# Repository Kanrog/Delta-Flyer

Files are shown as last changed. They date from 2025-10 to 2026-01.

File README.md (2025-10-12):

# Delta Flyer Refit Website

This is the website for the Delta Flyer Refit 3D printer project, designed by Rolohaun and Kanrog, with a building kit by LDO.
  
  <p style="margin: 18px 0;">
    <a href="https://kanrog.github.io/Delta-Flyer/" target="_blank" rel="noopener noreferrer" style="display:inline-block; text-decoration:none; padding:10px 18px; border-radius:8px; border:1px solid #ddd; background:#f7f7f7;">
      Open the live site → https://kanrog.github.io/Delta-Flyer/
    </a>
  </p>
  
## Credits

- **Design**: Rolohaun & Kanrog
- **Kit Manufacturer**: LDO
- **Website Template**: Based on Kanrog Creations website

## License

All content related to the Delta Flyer Refit project is subject to the original project's licensing terms.

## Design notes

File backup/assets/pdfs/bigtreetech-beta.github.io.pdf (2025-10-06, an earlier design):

DZ01

## Product Prole

The BIGTREETECH DZ01 is a powerful motherboard featuring the Allwinner H616 SoC, a quad-core

Cortex-A53 @1.5 GHz, with 1GB DDR3L RAM, and support for high-performance Klipper running. It

includes a 32-bit RP2040 MCU for precise multi-axis motion control, onboard TMC2209 drivers, Wi-

Fi connectivity, and 4K HDMI output, making it an all-in-one solution for your 3D printing projects.

## Feature Highlights

MCU: 32-bit ARM Cortex-M0+ series RP2040, running at 133MHz;

SoC: Allwinner H616, Quad-core Cortex-A53 @1.5GHz;

GPU: Mali G31 MP2, supports OpenGL 3.2;

RAM: 1GB DDR3L SDRAM;

Display Output: HDMI 2.0A, supports 4K monitors;

Two USB 2.0 ports;

Serial Port Output;

Networking: 100Mbps Ethernet + 100Mbps Wi-Fi;

Contains a TPS5450-5A power chip which supports DC12/24V power input. This chip provides

an output current of up to 5A, peaking at 6A;

A reserved BOOT button within the motherboard allows users to update the bootloader using

the DFU mode;

A specially designed circuit on the motherboard protects the signal coming back from the

thermistor, preventing MCU damage from shorted heated beds and heater cartridge

connections;

Users can upgrade the MCU rmware via an SD card, or update the MCU rmware through DFU

using the make ash command in Klipper;

Includes specic interfaces that are reserved for Filament Detection, Auto Power-Off, BLTouch,

RGB, etc.

High-performance MOSFETs assist in reducing heat generation by controlling the ow of

electrical current;

Includes replaceable fuses;

Proximity Switch Interface: Reserved;

SPI Expansion Interface: Reserved for connecting external accelerometers for Klipper input

shaping.

## Specications

Dimensions: 80mm*125mm

Mounting Dimensions: For details, please refer to BIGTREETECH DZ01.pdf

SoC: ALLWINNER H616, Quad-core Cortex-A53 @1.5GHz

MCU: 32-bit ARM Cortex-M0+ series RP2040 with a clock speed of 133MHz

Driver Input Voltage: 24V

Motherboard Input Voltage: VIN=DC12V or DC24V

Heated Bed Input Voltage: BED IN=DC12V or DC24V

Logic Voltage: DC3.3V

Heating Interface: Heating Interface: Heated Bed (HB), Heater Cartridge (HE0, HE1)

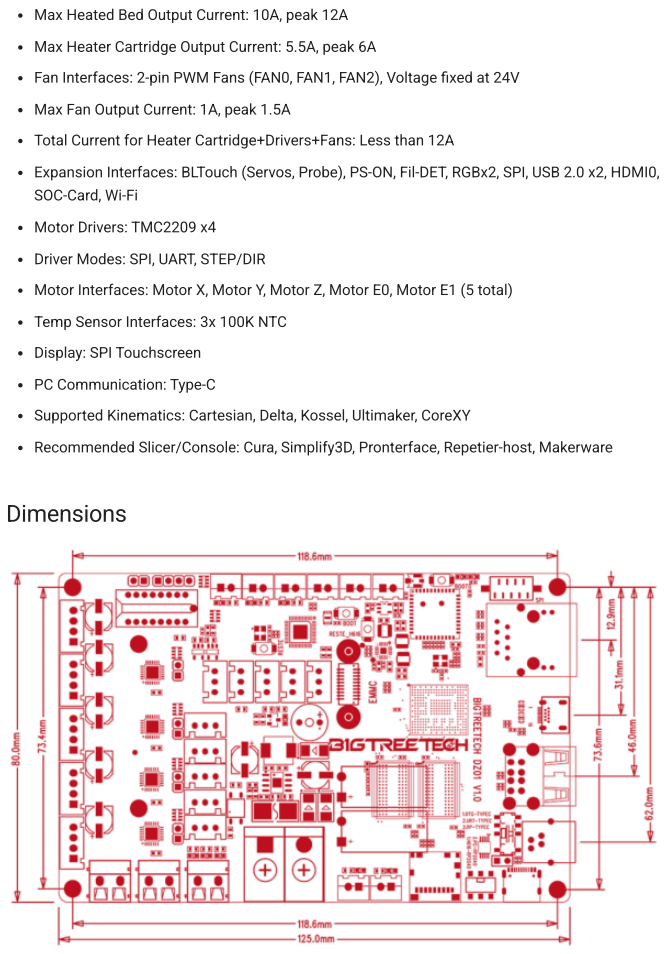
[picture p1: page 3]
Motor Drivers: TMC2209 x4; Dimensions

Max Heated Bed Output Current: 10A, peak 12A

Max Heater Cartridge Output Current: 5.5A, peak 6A

Fan Interfaces: 2-pin PWM Fans (FAN0, FAN1, FAN2), Voltage xed at 24V

Max Fan Output Current: 1A, peak 1.5A

Total Current for Heater Cartridge+Drivers+Fans: Less than 12A

Expansion Interfaces: BLTouch (Servos, Probe), PS-ON, Fil-DET, RGBx2, SPI, USB 2.0 x2, HDMI0,

SOC-Card, Wi-Fi

Driver Modes: SPI, UART, STEP/DIR

Motor Interfaces: Motor X, Motor Y, Motor Z, Motor E0, Motor E1 (5 total)

Temp Sensor Interfaces: 3x 100K NTC

Display: SPI Touchscreen

PC Communication: Type-C

Supported Kinematics: Cartesian, Delta, Kossel, Ultimaker, CoreXY

Recommended Slicer/Console: Cura, Simplify3D, Pronterface, Repetier-host, Makerware

## Peripheral Interface

### Interface Diagram

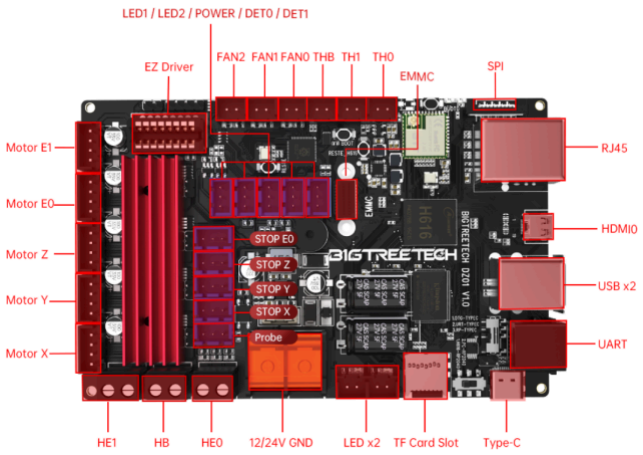
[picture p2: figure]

## Interface Introduction

### USB Power Supply

The power light on the upper left corner of the MCU turns red when DZ01 is powered on, indicating

a normal power supply. The VUSB power select pin needs to be shorted by placing the jumper over

the pin, however this is only necessary when a USB is required to supply power to the board.

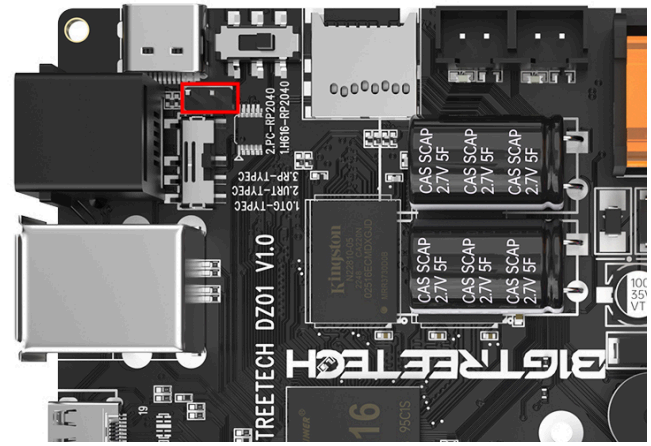
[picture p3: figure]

### SPI Interface

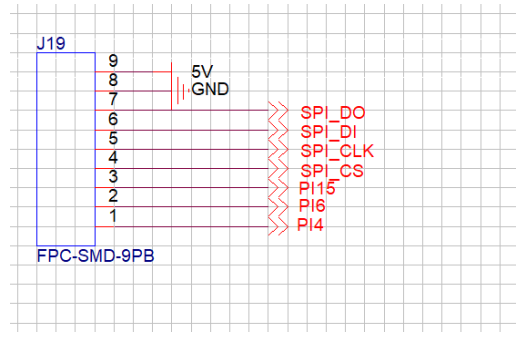
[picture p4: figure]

1. SPI_DO H616-PH8
2. SPI_DI H616-PH7
3. SPI_CLK H616-PH6
4. SPI_CS H616-PI14
5. SPI_RES H616-PI15

. SPI_SDA H616-PI6

7. SPI_SCL H616-PI4

### Serial Port Interface

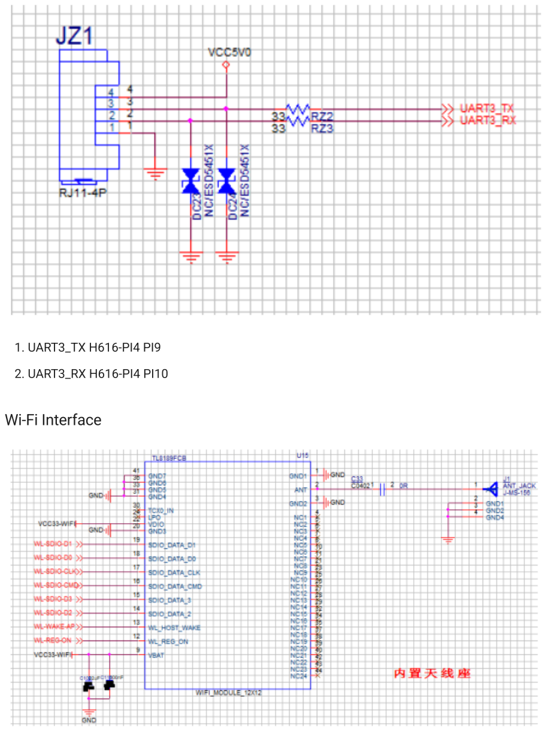
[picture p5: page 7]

1. UART3_TX H616-PI4 PI9
2. UART3_RX H616-PI4 PI10

### Wi-Fi Interface

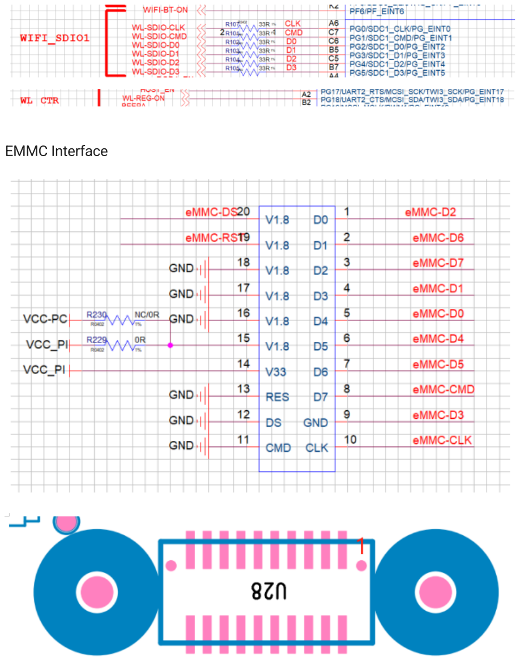
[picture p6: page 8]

### EMMC Interface

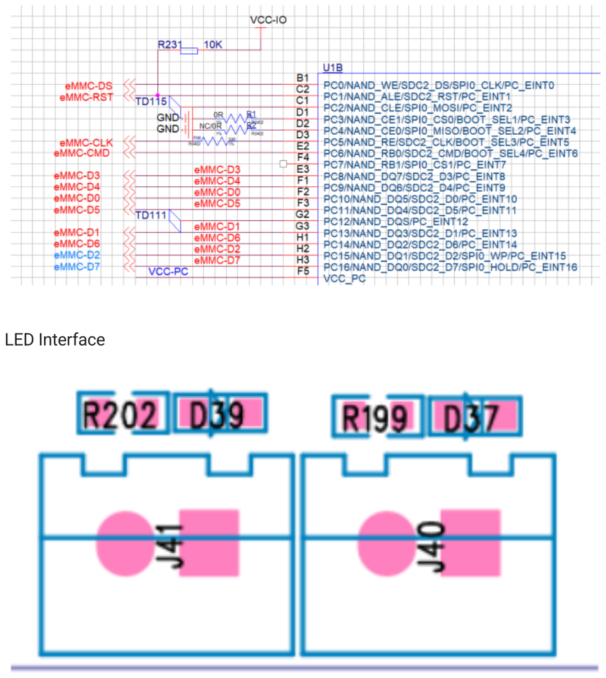
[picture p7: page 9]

### LED Interface

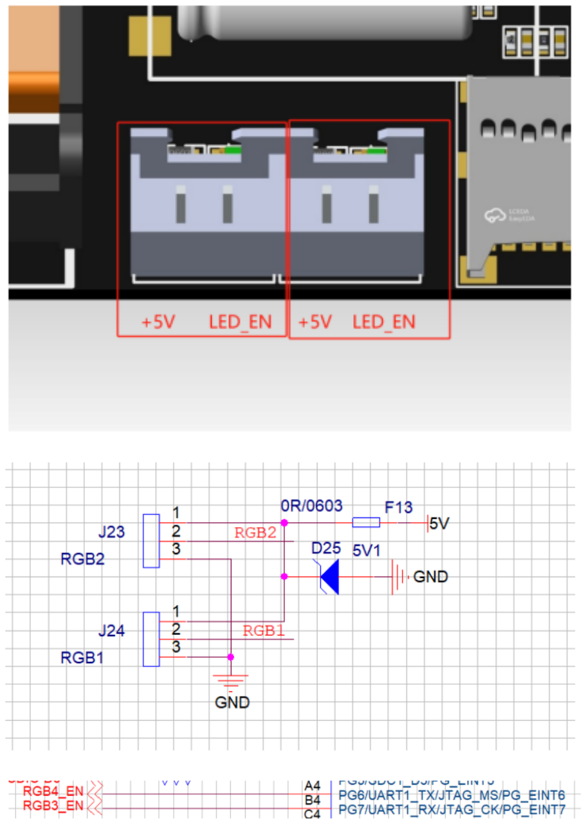
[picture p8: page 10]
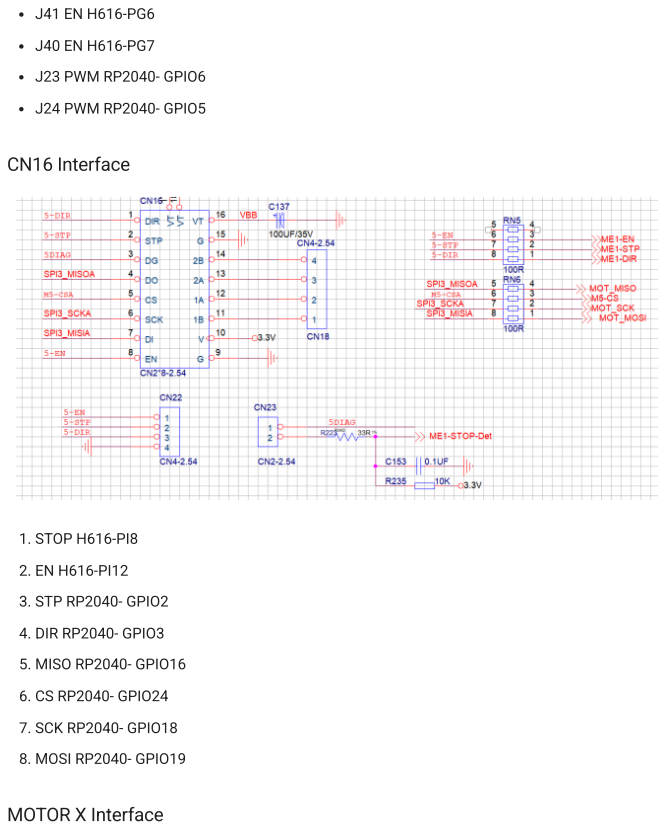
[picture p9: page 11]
J23 PWM RP2040- GPIO6; J24 PWM RP2040- GPIO5; CN16 Interface; 1. STOP H616-PI8; 3. STP RP2040- GPIO2; 4. DIR RP2040- GPIO3; 5. MISO RP2040- GPIO16; . CS RP2040- GPIO24; 7. SCK RP2040- GPIO18; . MOSI RP2040- GPIO19; MOTOR X Interface

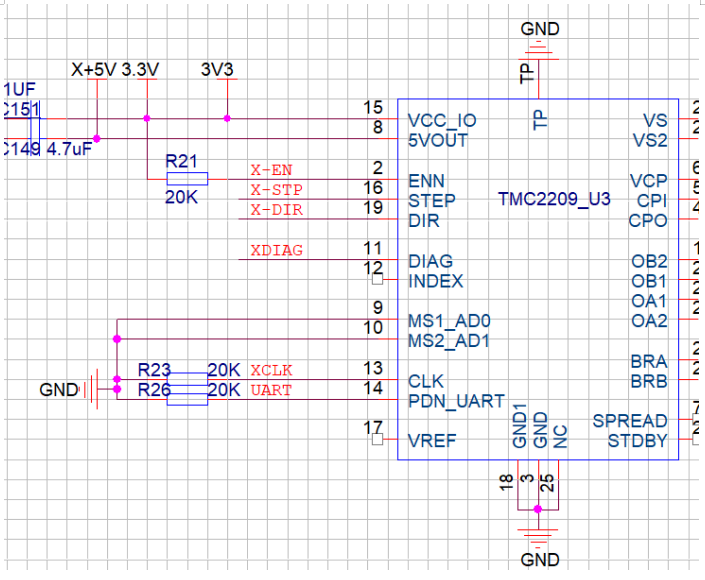
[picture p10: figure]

1. STOP H616-PI1
2. EN H616-PI3
3. STP RP2040- GPIO15
4. DIR RP2040- GPIO14
5. UART RP2040- GPIO0 TX/GPIO1 RX

### MOTOR Y Interface

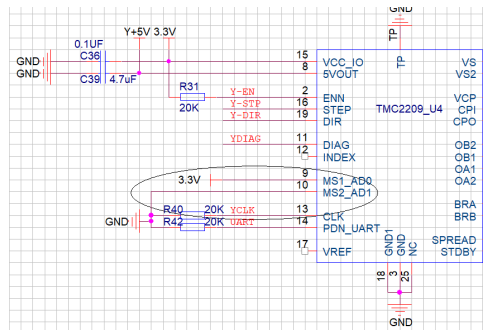
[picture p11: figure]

1. STOP H616-PI5
2. EN H616-PI0
3. STP RP2040- GPIO13
4. DIR RP2040- GPIO12
5. UART RP2040- GPIO0 TX/GPIO1 RX

### MOTOR Z Interface

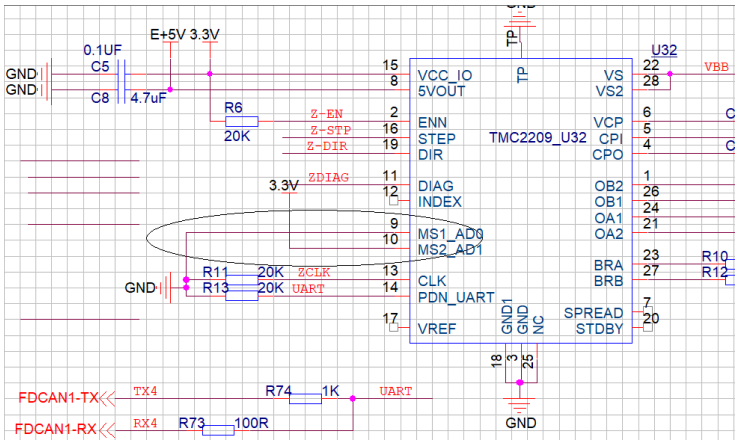
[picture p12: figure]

1. STOP H616-PI13
2. EN H616-PI7
3. STP RP2040- GPIO10
4. DIR RP2040- GPIO9
5. UART RP2040- GPIO0 TX/GPIO1 RX

### MOTOR E0 Interface

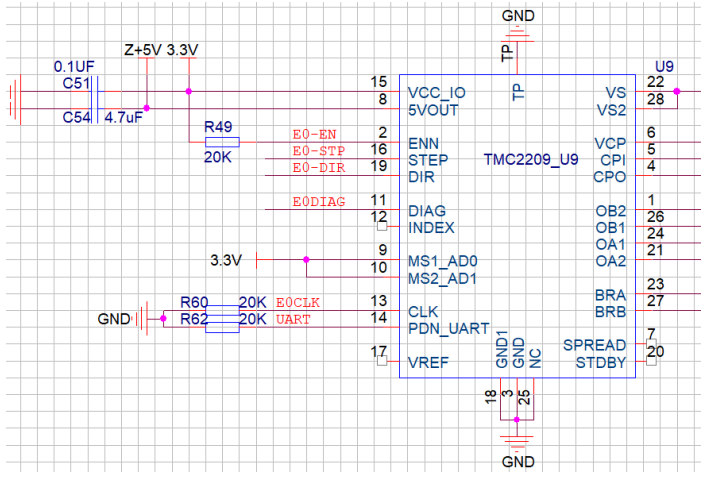
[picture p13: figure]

1. STOP H616-PI1
2. EN H616-PI2
3. STP RP2040- GPIO8
4. DIR RP2040- GPIO7
5. UART RP2040- GPIO0 TX/GPIO1 R

### MOTOR E1 Interface

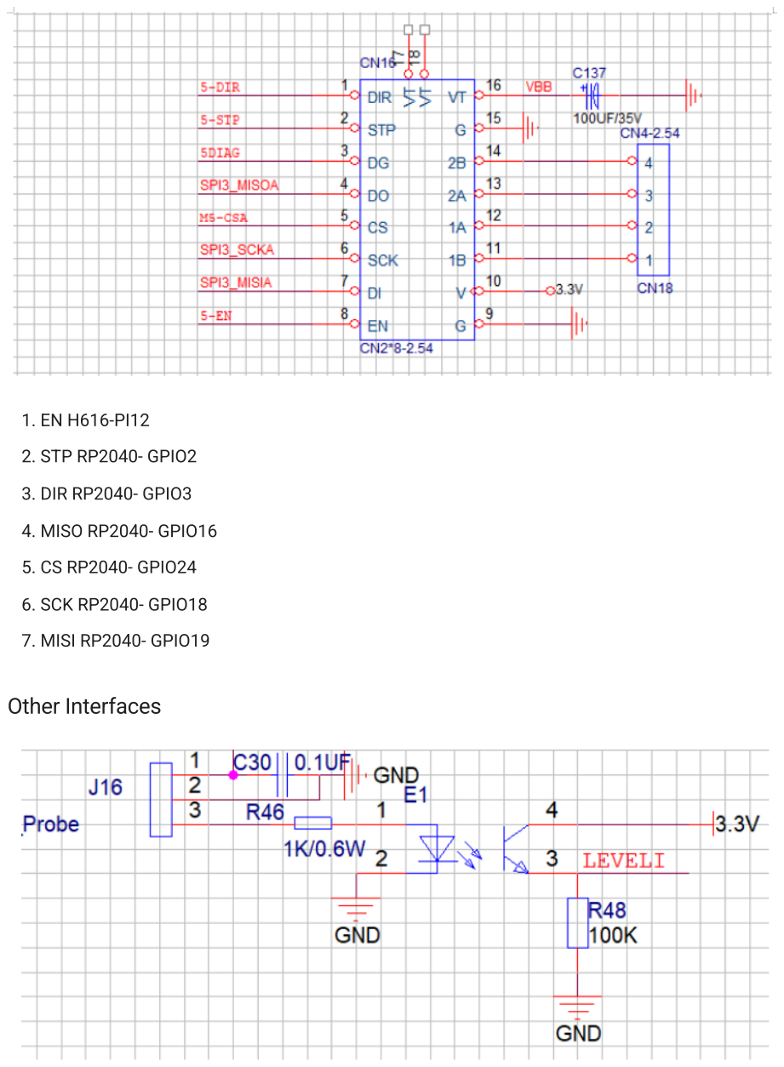
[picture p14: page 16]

1. EN H616-PI12
2. STP RP2040- GPIO2
3. DIR RP2040- GPIO3
4. MISO RP2040- GPIO16
5. CS RP2040- GPIO24

. SCK RP2040- GPIO18

7. MISI RP2040- GPIO19

### Other Interfaces

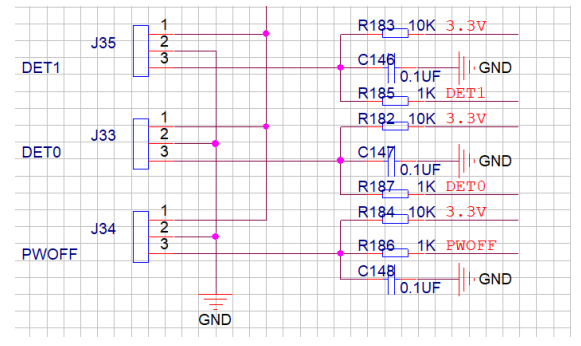
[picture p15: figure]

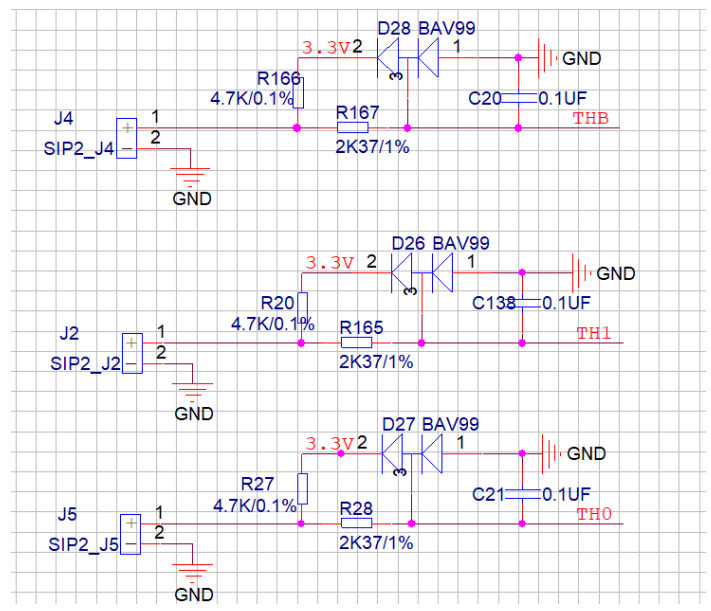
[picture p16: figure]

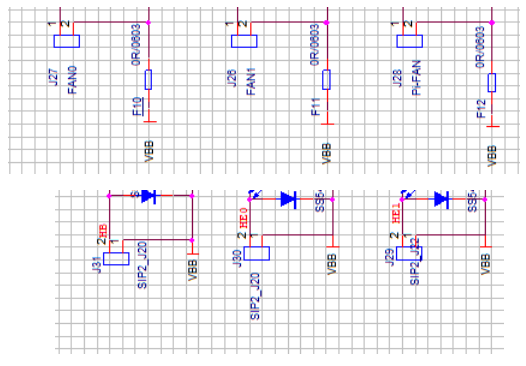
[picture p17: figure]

1. DET1 H616-PG11
2. DET0 H616-PG16
3. POWER RP2040- GPIO25
4. LEVELI RP2040- GPIO20
5. THB RP2040- GPIO28

. TH1 RP2040- GPIO27

7. TH0 RP2040- GPIO26

. FAN0 RP2040- GPIO29

9. FAN1 RP2040- GPIO4
10. FAN2 RP2040- GPIO11
11. HB RP2040- GPIO23
12. HE1 RP2040- GPIO22
13. HE0 RP2040- GPIO21

### Buzzer Interface

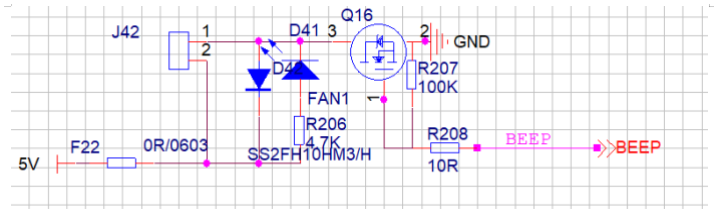
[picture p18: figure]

BEEP H616-PG19

### USB Power Supply Interface

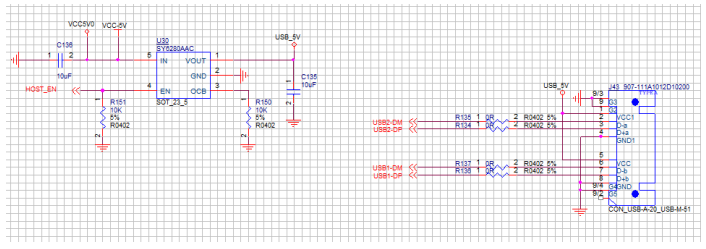
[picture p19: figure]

HOST_EN H616-PG17

### Battery Power Supply Interface

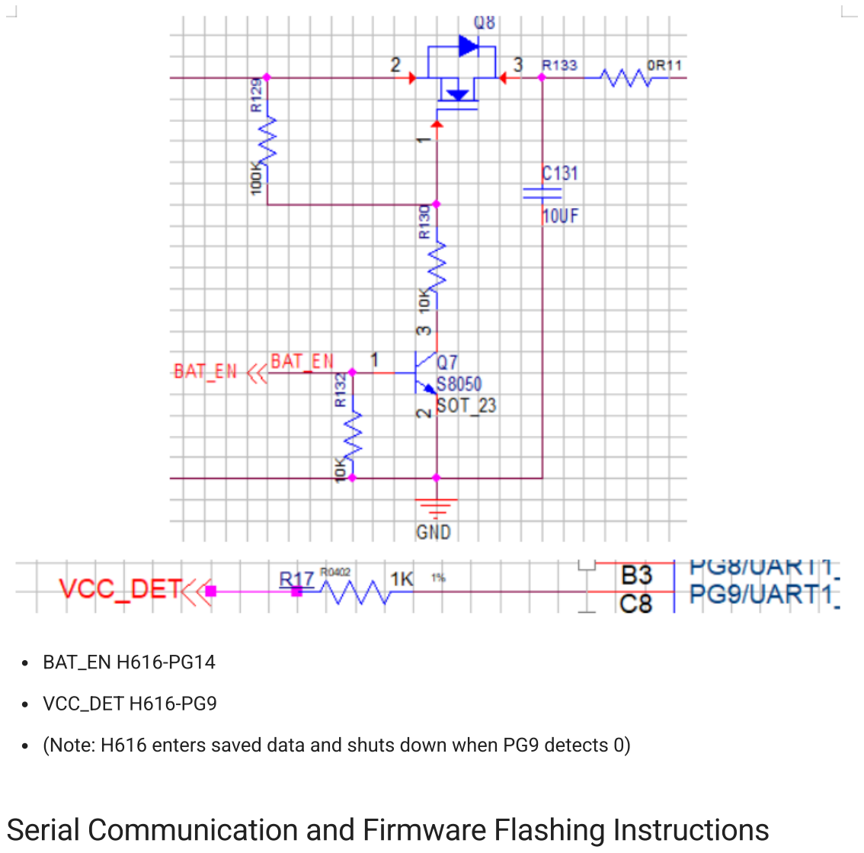
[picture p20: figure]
BAT_EN H616-PG14; VCC_DET H616-PG9

(Note: H616 enters saved data and shuts down when PG9 detects 0)

## Serial Communication and Firmware Flashing Instructions

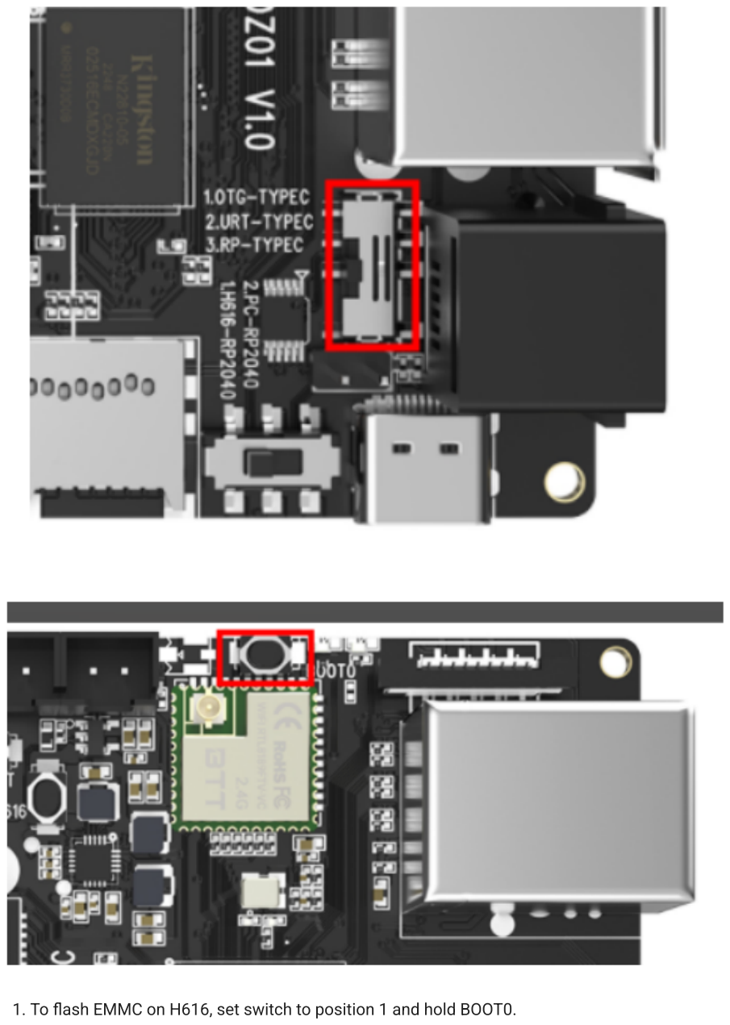
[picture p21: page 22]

1. To ash EMMC on H616, set switch to position 1 and hold BOOT0.

2. For serial output on H616, set switch to position 2.
3. To ash RP2040, set switch to position 3, and set switch 2 to PC-RP2040.
4. For communication between RP2040 and H616, set switch 2 to H616-RP2040.

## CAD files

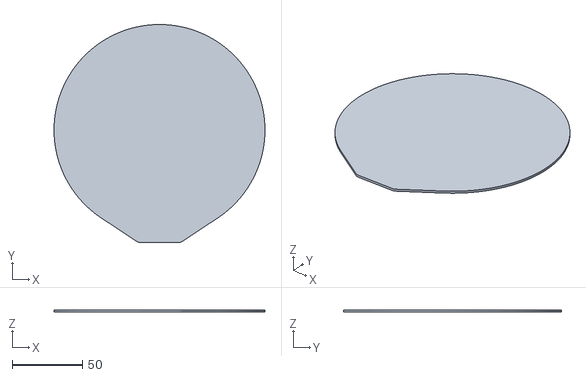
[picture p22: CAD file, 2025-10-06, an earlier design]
backup/assets/configs/Delta_Flyer_Buildplate_150.stl
150.0 x 155.0 x 1.50

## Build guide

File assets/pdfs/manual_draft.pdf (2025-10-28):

# LDO Rolohaun Delta Flyer Build manual (rough draft)

## There is a more detailed but incomplete version HERE if you prefer that. (https://kanrog.github.io/Delta-Flyer/manual-draft.html)

1. Glue the arms together, use the M3x30 threaded rods, keep the joints oriented identical on each end.
2. Prepare the printed parts by removing all the built in supports.
a. Top_Frame(middle)

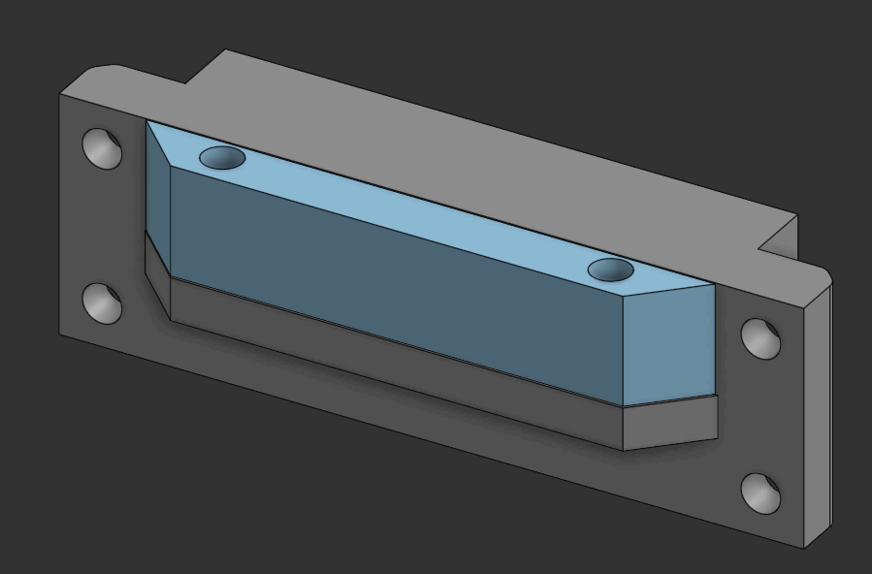
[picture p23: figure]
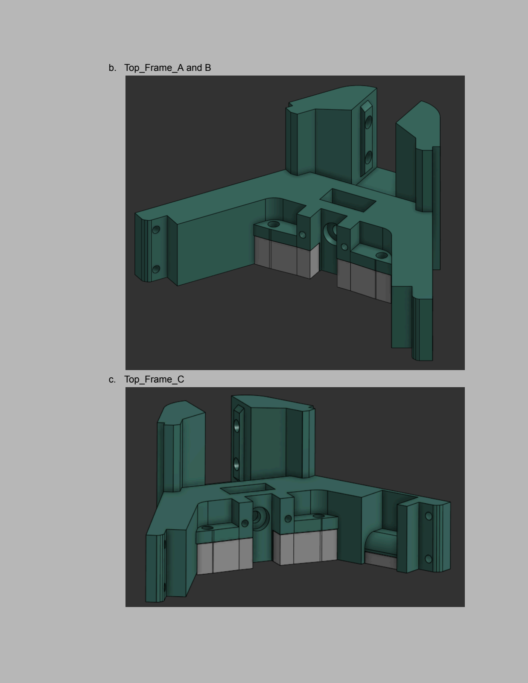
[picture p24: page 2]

b. Top_Frame_A and B
c. Top_Frame_C

d. Carriage

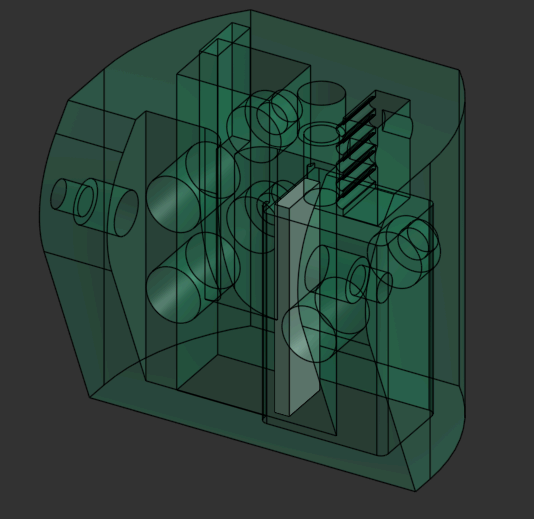
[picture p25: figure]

3. Insert headsets into the following pieces:

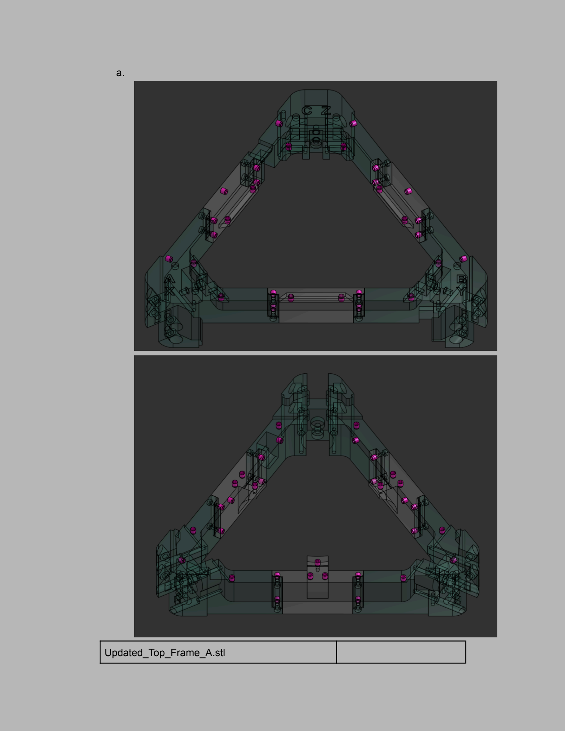
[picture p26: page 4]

a.

Updated_Top_Frame_A.stl

Updated_Top_Frame_B.stl

Updated_Top_Frame_C.stl

Updated_Bottom_Frame_A.stl

Updated_Bottom_Frame_B.stl

Updated_Bottom_Frame_C.stl

Updated_Top_Frame_Middle.stl

2 x Updated_Top_Frame_side_with_support.stl

2 x Updated_Bottom_Middle.stl

Updated_Bottom_Frame_Center.stl
b.

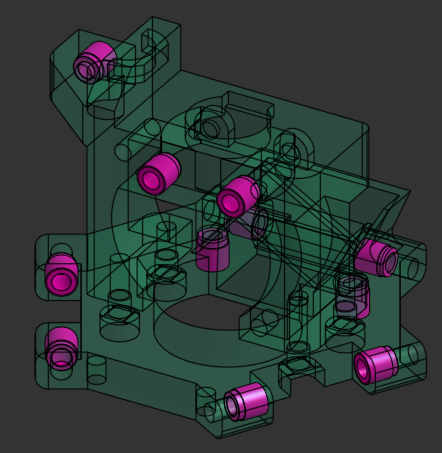
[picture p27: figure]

Effector.stl

TR6_Hotend_Mount_LDO.stl

c.

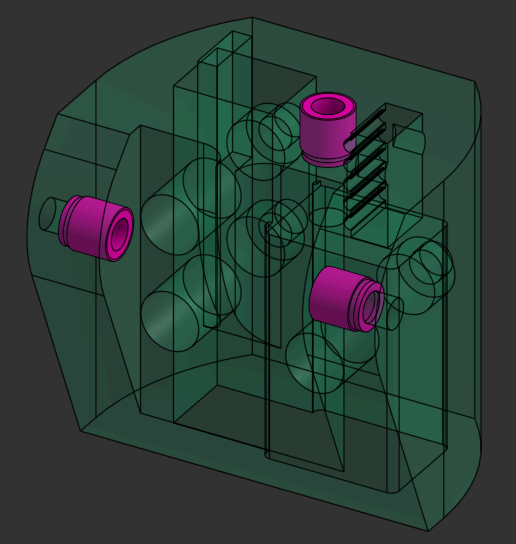
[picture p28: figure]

3 x Tensioner.stl

d.

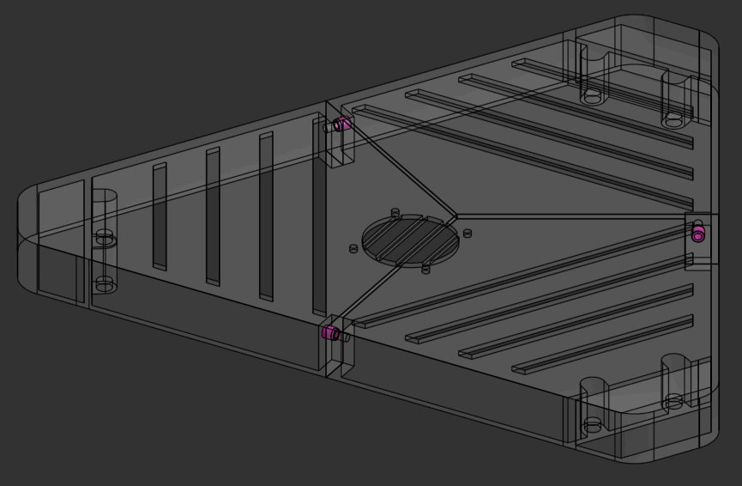
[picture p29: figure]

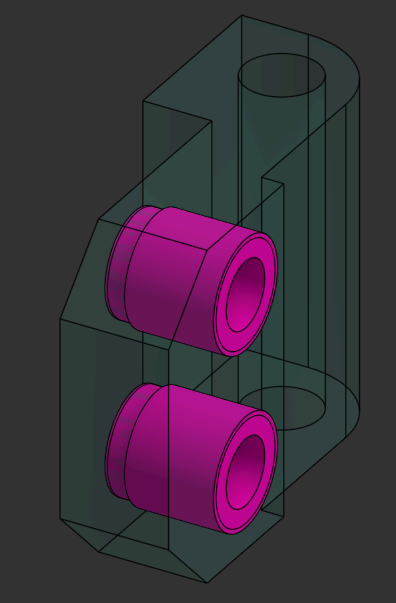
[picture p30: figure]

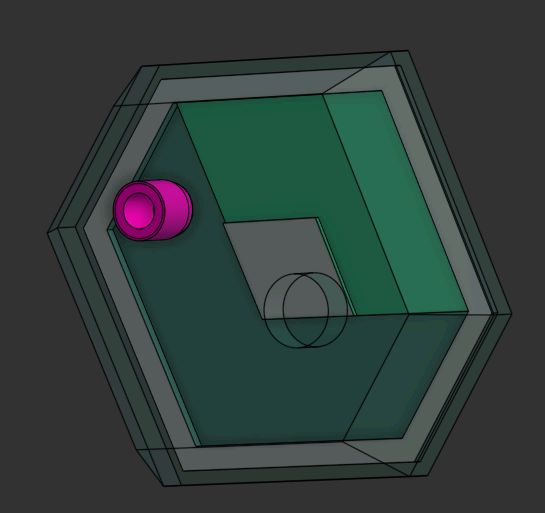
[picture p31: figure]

Top_Cover_A.stl

Top_Cover_B.stl

Top_Cover_C.stl

Handle.stl

2 x Hinge.stl

4. Start by assembling each upright corner.
a. Insert the F695 bearings into the lower frame corners, put the GT2 pulley on the motor, setscrew towards the motor. Attach the motor to the frame corner using 4xM3x30 screws.
b. On the top frame corners, attach the GT2 idler with a M5x16 screw, then attach the optical endstop with the black protrusion in toward the M5 screwhead using 2xM3x12 screws.
c. Attach the 2020 extrusion to the top frame corner using 4xM5x10 screws and T-nuts then attach the MGN9 rail using 5xM3x8 screws and t-nuts.

d. Attach the 4 corner panel pieces to each upright, but do not attach the two front corner panels on the “B” corner, these are attached later after the doorhinges. The front lower panel cover on the “A” upright has a hole for a magnet.
e. Finally, attach the bottom corner piece to the extrusion using 4xM5x10 screws and t-nuts.
f. Attach the carriages to the MGN9 rails using 3xM3x6 screws.
g. Using the Apex clips, fasten the belt to the tensioner, put the tensioner into the carriage(apex clip down) and route the belt down around the pulley, back up through the carriage, around the top idler and back into the carriage, attached with another apex clip. Use a M3x30 screw to tension the belt to the carriage.
5. Bolt the frame together, remember to have the middle frame pieces without headsets on the outside towards the front.
6. Add the small sticky feet to the bottom of the frame.
7. Attach the heated bed to the frame using 3xM3x16 screws and 3xM4 thumbscrews as spacers between the bed and the frame.(I am not sure the state this arrives in, let me know)
8. Attach the 3 motor covers using M3x6 screws, note the one with the notch goes on the back “C” corner.
9. Attach the top electronics panels, these are marked. Text goes up.
10. Attach the TR6_hotend_mount to the Effector using 4xM3x8 screws.
11. Attach the hotend to the TR6_hotend_mount using 2xM3x16 screws.
12. Attach the 3010 hotend fan using 3xM3x16 screws.
13. Route the hotend and 5015 fan wires through the cable relief hole on the left side and attach the 5015 fan using a M3x20 screw.
14. Bolt the effector to the carriages using the arms and 12xM3x20 screws.
15. Attach the back left panel, then attach the BMG to it using 2xM3x10 screws and heatinserts as nuts on the inside. Good time to put the PTFE in. (cut to length)
16. Prepare the top electronics cover by bolting it together using 3xM3x8 screws and gluing in the 6 magnets. Now is also a good time to glue in the magnets on the top frame, keeping polarization in mind.
17. Install the DZ01 board in the electronics bay using 4xM3x6 screws.
18. Install the RGB strip to the inside of the chamber using 2 zipties on the top cover.(labeled)
19. Connect all the wires according to the wiring diagram. (https://kanrog.github.io/Delta-Flyer/assets/pdfs/Delta_Flyer_Wiring_Diagram.pdf)
20. Install klipper on the DZ01 and run through the first setup process using the install manual. (https://kanrog.github.io/Delta-Flyer/klipper-tutorial.html)
21. After initial setup, put in the 2 wire covers on the inside of the left panel using 8xM3x6 screws.
22. Install the right panel and finally the door, front right panel covers and doorhinges(2xM3x20 screw freely floating inside the hinge and the panel covers. Also install the doorhandle and glue in the 2 magnets for it.
23. Attach the spool holder on the back using 2xM3x8 screws, use some of the leftover PTFE tube in the spool holder arm. You can attach the power cable hook using M3x8 screws too, one on the top, one on the bottom, facing to the right side of the printer.

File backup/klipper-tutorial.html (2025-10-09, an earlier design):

# Rolohaun LDO Delta Flyer Refit

Software and First Print Tutorial

By Kanrog Creations

### Delta Flyer Refit - Wiring Reference

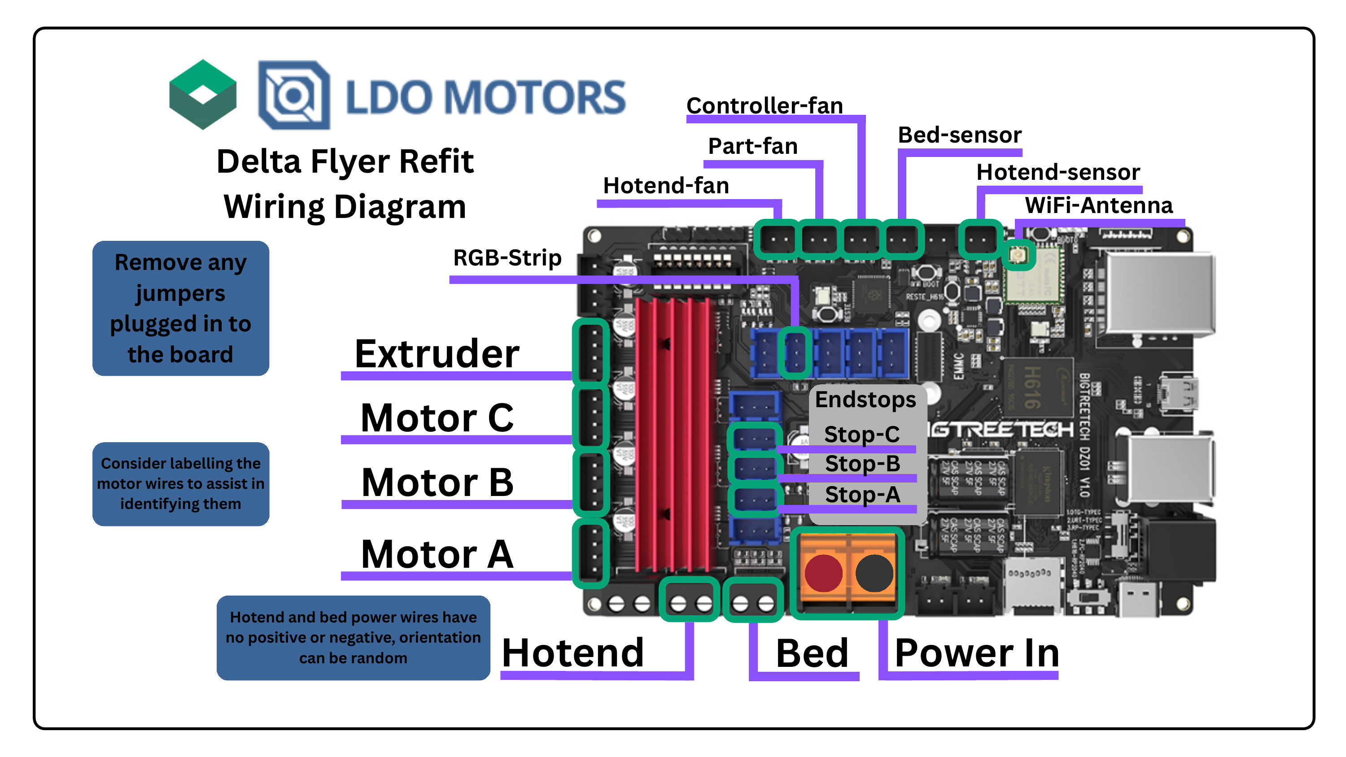
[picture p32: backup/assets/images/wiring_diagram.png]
Delta Flyer Refit Wiring Diagram


## 1. Notes

ℹ️

Optional Tutorial

#### Klipper Compatibility

The klipper-section of this tutorial is a general guide to installing Klipper on the DZ01, and can be used for pretty much any printer using that board, not just the Flyer.

📁

Config Files

#### Board Compatibility

The config files used are specifically for the LDO Delta Flyer kit using a DZ01, if you are using a different board, the config files will not work, but the macros should work on any Flyer setup.

## 2. Step-by-Step Process/Content

1

Download Software and Files

Essential tools and files for setup

To complete this tutorial, we need Balena Etcher or another Imaging tool like pi imager or Win32DiskImager. I won't cover installing these, but it should be pretty straight forward.

#### Balena Etcher

Image flashing tool for SD cards

https://etcher.balena.io/

#### Angry IP Scanner

Network device discovery tool

https://angryip.org/download/#windows

#### CB1 Image

Bigtreetech CB1 firmware image

https://github.com/bigtreetech/CB1/releases

#### OrcaSlicer

3D printing slicer software

https://github.com/SoftFever/OrcaSlicer/releases

#### Config Bundle

Kanrog Creations configuration files

https://github.com/Kanrog/Delta-Flyer-Refit

To find our device on the network, I'll be using a software called "Angry IP Scanner", they have a portable version that wont need to be installed on your computer, let's download that.

Next we need the image to put on the micro SD going into the CB1, this can be downloaded from Bigtreetech's Github, I recommend getting the larger of the two versions.

To slice our 3D models for printing, we will be using Orcaslicer. You can download the latest build from their github.

Finally, we are going to download the config bundle from the Kanrog Creations Github, ready to transfer over to our Flyer.

2

Burn CB1 Image

Flashing and configuring the CB1 board

Insert the micro SD card into your computer, open Balena Etcher(or another imaging tool of your choice), select the CB1 image we downloaded, Select the micro SD card as a target and press "Flash!". This will take a few minutes.

Next, pull the SD card out and put it back into the computer, navigate to it in the file explorer and find the file called system.cfg, and open it in a text-editor.

#### WiFi Configuration

In this file, find the "WIFI_SSID" line and add your wifi-SSID, next, go to the "WIFI_PASSWD" line and enter your Wifi's password, make sure to keep the apostrophes. Then save and close this file, pull the SD from your computer, and put it into the microSD slot on the M4P. Remember, the CB1 can only connect to 2.4GHz Wifi.

We can also set a custom name for this printer on the network by changing the line at the top that says: "#hostname="BTT-CB1"" into "hostname="DELTA-FLYER""

#### Important Note

(Remember to uncomment the line by removing the "#") Any name works, avoid spaces. Remember to save.

Remove the SD card and insert it into the DZ01.

Now we are ready to power up the printer for the first time! Just take a minute and make sure you don't have any loose wires and that everything is connected somewhere.

Boot up the printer and give it a little time to do its initial boot, this takes longer the first time, normally not longer than 5-10 minutes.

After the printer has booted up, we need to find the IP of the printer, there are a couple ways to do that, usually by logging in to your wifi-router, but this is different depending on what router you have, so I will be using a different method; the Angry IP scanner we downloaded earlier.

Open the ipscan_win64-xx.exe we downloaded earlier and hit "Start". Let it finish the scan, and when it's done, it will give you a prompt saying "Scanning Complete". Click close.

Now we can sort the list by "Hostname" and look for our CB1, it should show up as the name you set earlier in the list. If not, look for an IP using the port "80". Now we have the IP for our printer!

To make sure everything is working, let's open this IP in a browser and see if we can connect to the printer that way first.

While we are in here, let's do some cleanup and get ready to transfer the config files. Go to the "Machine" tab and press the "Create Directory" icon. Let's call this folder "Old" because we are going to put all the files that we don't need in here.

Now, lets move some files into this folder by simply dragging them in, lets move the [printer.cfg] and [print_area_bed_mesh.cfg] files. We do this mostly as a good habit. There's nothing worse than deleting something and realizing you need it later.

After clearing up some space, we can open the config bundle in a file explorer and drag the printer.cfg into the mainsail browser-window, this will copy it onto our printer.

Press "Save and Restart" at the top of the window and then power cycle the printer.

#### Success!

Your printer should now be up and running!

3

Macros

Setting up helpful automation macros

I've included a set of macros that will help you get going. If you are like me, you can sort them to make things a little more organized.

4

Delta Calibrate

Calibrating the delta motion system

Lets get the delta motion system calibrated; Press the macro called "ENDSTOPS CALIBRATION". The printer will home itself and start the built in endstop calibration tool, After it is done, press the "SAVE AND RESTART" button at the top of the screen.

Now we will make sure the effector (toolhead) moves parallel to the bed using the good old paper method. Press the "DELTA CALIBRATE MANUAL" macro and use the on-screen tool that pops up to adjust each of the 7 points on the bed. To do this, place a piece of paper between the nozzle and the bed and slowly lower the toolhead using the "-" button until you feel resistance on the paper. Now fine tune it so that you can move the paper, but still have a little resistance and press "ACCEPT" when you are happy. Repeat until the tool is complete. (the amount of resistance isn't important, just make sure it's the same amount across all points)

After it is done, press the "SAVE AND RESTART" button at the top of the screen.

5

PID

Calibrating heater controllers

We want to calibrate our heaters. To do this, simply use the respective macros, "PID HOTEND" and "PID HEATBED". The printer will save and restart after each of them. This will take a while.

6

Orcaslicer Setup

Configuring the slicer software

Install and open Orcaslicer. (Needs to be V2.3.1 or newer)

In the window that appears, press "Get started" and find the RolohaunDesign Delta Flyer, select 0.4 nozzle (if you have a stock setup) and press "Next".

In the next window, we can select the filament types we want to have available. The Delta Flyer can print PLA, PETG, ABS, TPU and PC. Press "Next".

Enable stealth mode and press "Next".

Enable "Install Bambu Network plug-in" and press "Next". Let it install and click "close".

Navigate to the "Prepare" tab, press the little Wifi button next to the name of the printer, find the "Hostname" box and enter the IP used to open Mainsail in your browser, press "enter" and "Test" to make sure the connection works. Give your printer a name at the top and press "OK".

#### Connected!

You now have access to mainsail directly in the slicer in the "Device" tab!

7

First Print!

Z-offset calibration and test printing

For our first print, we are going to do a Z-offset fine tune, as well as check our leveling.

To do this, Right click the build-area in OrcaSlicer, navigate to "Add Primitive" -> "Cylinder".

With the cube selected, press the "Scale" tool on the top toolbar and uncheck "Uniform scale", enter 80,80 and 0.2 in the "size" boxes.

At the top bar, press "Slice plate"

Insert filament into the extruder, navigate to the "Device" tab, and press the "Load Filament" macro, this should pull the filament all the way to the hotend.

Back in the "Preview" tab in OrcaSlicer, press "Print" followed by "Upload and Print" This will send the file to your printer and automatically start the print.

Go to the "Device" tab again and make sure your printer is heating up and getting ready to print.

When the print starts, use the "Z-Offset" tool in the "Toolhead" window to adjust the height of your hotend to the bed until you have a nice and smooth first layer, with no gaps between the lines.

Repeat the print if needed. When the first layer looks good, press "SAVE"(in the z-offset window) and "SAVE CONFIG".

You are now ready for your first ACTUAL print. I recommend downloading the "Rolo Cube" from Printables and print as your first print. It's a good way to ensure your printer works as it should, and is a great opportunity to make a short little video to upload to Youtube for your serial application!

## 3. Recap & Conclusion

## 🎉 Congratulations!

If you have any issues during the setup, please reach out to us on the Rolohaun discord.

Join Rolohaun Discord (https://discord.gg/5F9M6Ty3)

At this point, you have a printer you can enjoy, print what your heart desires!

### Return to Delta Flyer Refit

Ready to explore more resources and configuration files?

← Back to Main Site

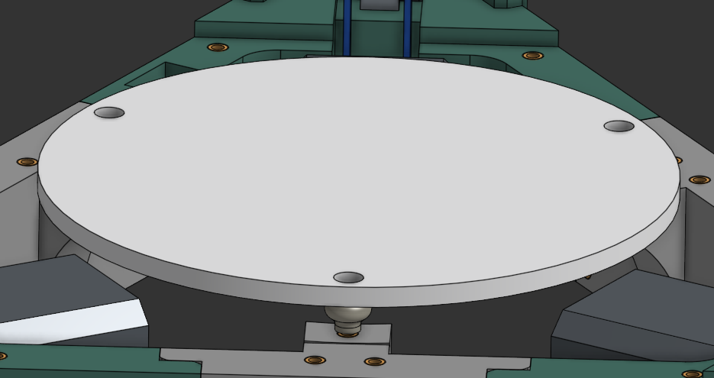
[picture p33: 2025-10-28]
assets/images/manual/21.png

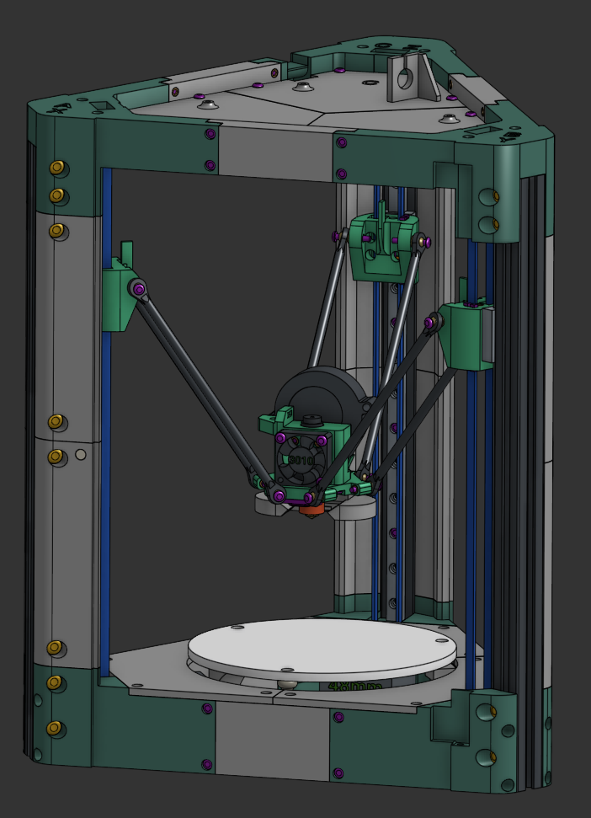
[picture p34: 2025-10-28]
assets/images/manual/29.png

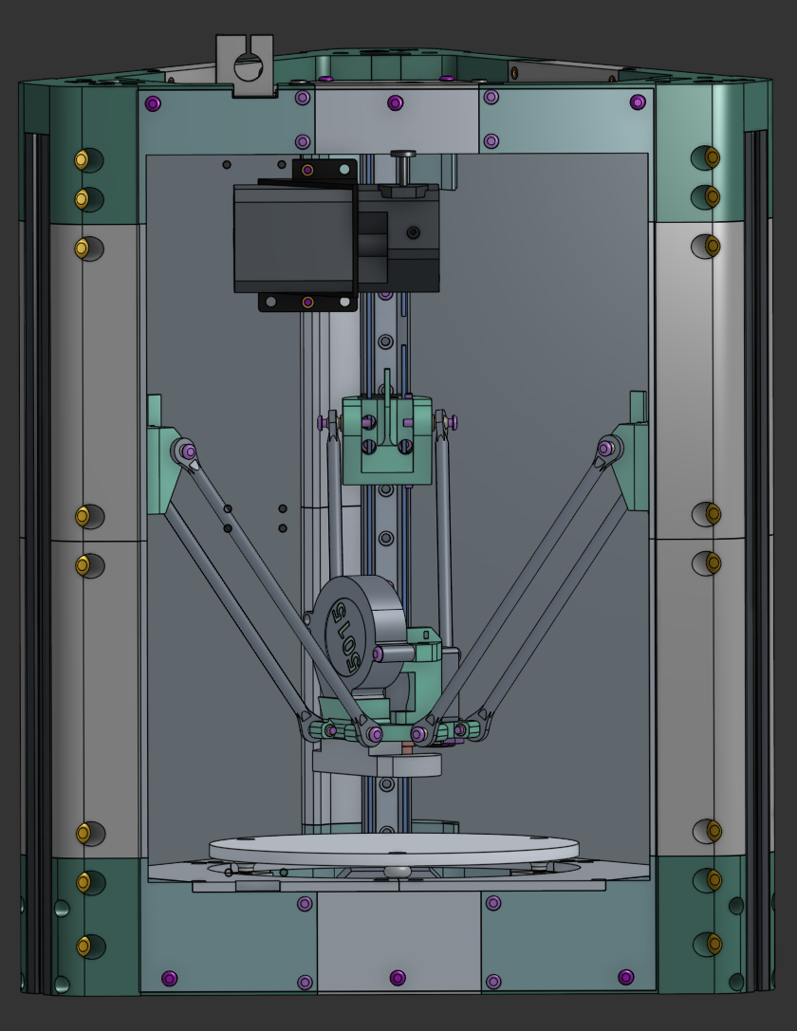
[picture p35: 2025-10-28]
assets/images/manual/30.png

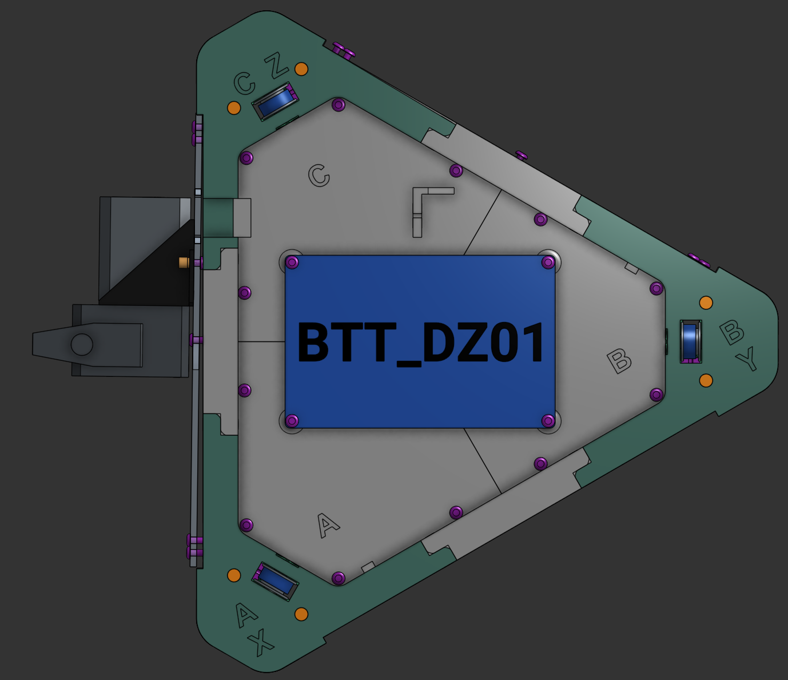
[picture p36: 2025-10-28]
assets/images/manual/32.png

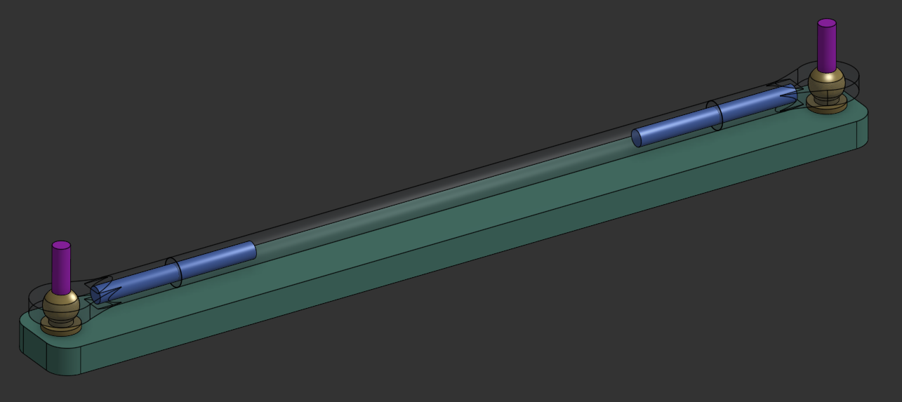
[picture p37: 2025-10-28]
assets/images/manual/8.png

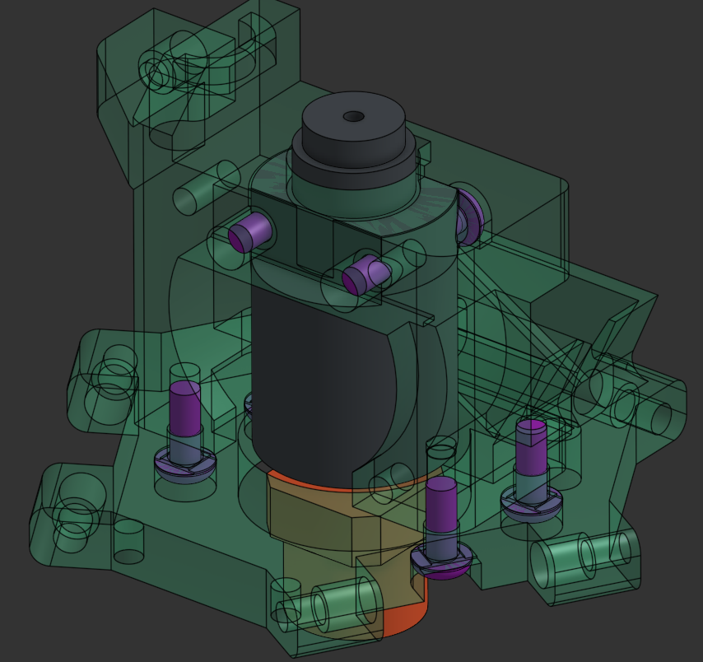
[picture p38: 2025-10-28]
assets/images/manual/25.png

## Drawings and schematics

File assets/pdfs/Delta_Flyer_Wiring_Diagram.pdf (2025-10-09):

## Delta Flyer Refit Wiring Diagram

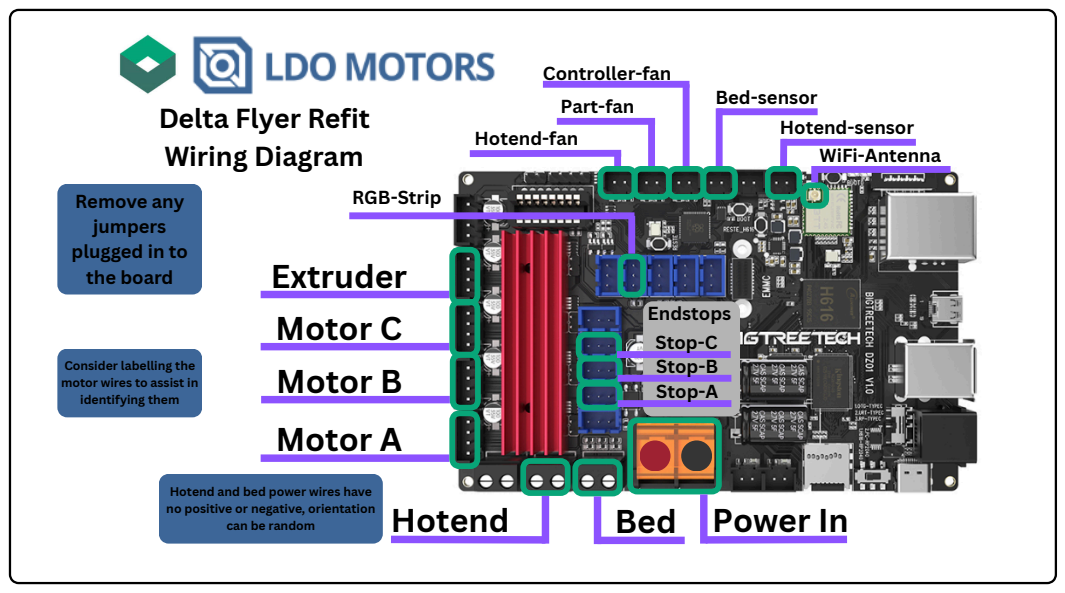
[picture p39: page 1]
Motor A; Motor B; Motor C; Extruder; Hotend; Bed; Power In; Hotend-fan; Part-fan; Controller-fan; Bed-sensor Hotend-sensor; Remove any; RGB-Strip; Endstops; Stop-A; Stop-B; Stop-C; WiFi-Antenna

jumpers
plugged in to
the board

Consider labelling the
motor wires to assist in
identifying them

Hotend and bed power wires have
no positive or negative, orientation

can be random

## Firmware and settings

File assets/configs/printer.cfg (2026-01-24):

#===========================================================================#
#===================#          DELTA FLYER REFIT        #===================#
#===========================================================================#
#===================#         Config by KANROG87        #===================#
#===========================================================================#

# If you have built the Delta Flyer from the LDO kit, this file should not need any changes made.
# However, reading trough it might be a useful tool in understanding your printer better.

# The following macros are supplied to simplify initial setup, they should be run once
# the printer is fully assembled and complete to calibrate the machine, this only needs to be done once.
# Do these macros in this order: (Just press the buttons in the main window)
# ENDSTOPS_CALIBRATION - Calibrates the endstops to increase the precision.
# DELTA_CALIBRATE_MANUAL - Ensures that the motion system is paired up to the bed, uses the "paper method"
# PID_HOTEND, PID_HOTBED. - Calibrates the heaters, these auto-saves and restarts the printer when they are done.

# You can edit macro-visibility in the webUI by using the "macro expert mode", I explain it in detail in this video: https://youtu.be/-WJzviqmzug?si=ztgtrfdlcF1ZA3tG

# This file contains all parameters klipper needs for the printer to work.
# It might seem daunting, but dont worry, you should not have to make any changes for your delta flyer to function properly.
# If you want to learn more about what each section does, I've included links to the klipper website for each topic and added notes to some of the lines to help explain their function.

#==================================#
#   INCLUDES
#==================================#
# These lines makes sure that klipper
# can read the extra files we imported,
# we do this to keep this file clean
# and easier too work on.

# MORE INFO:  https://www.klipper3d.org/Config_Reference.html#include
[include mainsail.cfg]

#==================================#
#   MCU
#==================================#
# These lines identifies the components
# that runs klipper and the printer.

# MORE INFO:  https://www.klipper3d.org/Config_Reference.html#mcu
[mcu] # Printer controller 
serial: /dev/serial/by-id/usb-Klipper_rp2040_h616-if00

[mcu h616] # SOC
serial: /tmp/klipper_host_mcu

#==================================#
#   Printer Limits
#==================================#
# These lines sets the limits of the
# printer, but they can be overwritten
# by other features.

# MORE INFO:  https://www.klipper3d.org/Config_Reference.html#printer
[printer] # This sets the printers parameters and limits. Note that the max speed and accel numbers set here can be overwritten by the slicers settings.
kinematics: delta
max_velocity: 400
max_accel: 10000
max_z_velocity: 100
max_z_accel: 100
delta_radius: 60
minimum_z_position:-1 # When doing the "DELTA_CALIBRATE" process, if you are not able to lower the nozzle down to the bed, set this number to something lower, like -3.

# MORE INFO:  https://www.klipper3d.org/Config_Reference.html#force_move
# [force_move]
# enable_force_move: True

# MORE INFO:  https://www.klipper3d.org/Config_Reference.html#stepper:~:text=positions%20and%0A%23%20angles.%0A%5B-,delta_calibrate,-%5D%0Aradius%3A%0A%23%20%20%20Radius%20(in
[delta_calibrate]
radius: 50 # This number sets the radius of the points used in "DELTA_CALIBRATE"
horizontal_move_z: 20 # how far up the nozzle moves from the bed on each point. you can lower this number to speed up the "DELTA_CALIBRATE" process

#==================================#
#   STEPPER A
#==================================#
# These lines sets all the parameters
# for the motors and the movement
# limits. these wont need to change
# unless you are installing a mod
# that changes any part of the
# movement of the printer.

# MORE INFO:  https://www.klipper3d.org/Config_Reference.html#stepper
[stepper_a]
step_pin: gpio15
dir_pin: gpio14 # If for some reason the motor is moving in the oppsite direction of what its supposed to, change this to "!gpio14"
enable_pin: !h616:gpio259 # H616-PI3
microsteps: 32
rotation_distance: 40
full_steps_per_rotation: 400
#   The number of full steps for one rotation of the stepper motor.
#   Set this to 200 for a 1.8 degree stepper motor or set to 400 for a
#   0.9 degree motor. The default is 200.
endstop_pin: ^h616:gpio267 # H616-PI1  E0
homing_speed: 80
position_endstop: 142 # If you are building a taller or shorter Delta Flyer, change this to fit your build size.
arm_length: 150
angle: 221 #212.689114
homing_retract_dist: 10
second_homing_speed: 5

# MORE INFO:  https://www.klipper3d.org/Config_Reference.html#tmc2209
[tmc2209 stepper_a]
uart_pin: gpio1
tx_pin: gpio0
run_current: 0.9 # This sets the amunt of power sent to the motor. If your motors are too hot, lower this value, if the motor is skipping steps, increase the value. Make sure this wont go too high, it can damage components.
interpolate: true
uart_address: 0
#stealthchop_threshold: 999999 # Uncomment to enable Stealthchop

#==================================#
#   STEPPER B
#==================================#

# MORE INFO:  https://www.klipper3d.org/Config_Reference.html#stepper
[stepper_b]
step_pin: gpio13
dir_pin: gpio12  # If for some reason the motor is moving in the oppsite direction of what its supposed to, change this to "!gpio12"
enable_pin: !h616:gpio256 # H616-PI0
microsteps: 32
rotation_distance: 40
full_steps_per_rotation: 400
#   The number of full steps for one rotation of the stepper motor.
#   Set this to 200 for a 1.8 degree stepper motor or set to 400 for a
#   0.9 degree motor. The default is 200.
endstop_pin: ^h616:gpio261 # H616-PI5
homing_speed: 80
position_endstop: 142 # If you are building a taller or shorter Delta Flyer, change this to fit your build size.
angle: 330 #329.987282
arm_length: 150
homing_retract_dist: 10
second_homing_speed: 5

# MORE INFO:  https://www.klipper3d.org/Config_Reference.html#tmc2209
[tmc2209 stepper_b]
uart_pin: gpio1
tx_pin: gpio0
run_current: 0.9 # This sets the amunt of power sent to the motor. If your motors are too hot, lower this value, if the motor is skipping steps, increase the value. Make sure this wont go too high, it can damage components.
uart_address: 2
#stealthchop_threshold: 999999 # Uncomment to enable Stealthchop

#==================================#
#   STEPPER C
#==================================#

# MORE INFO:  https://www.klipper3d.org/Config_Reference.html#stepper
[stepper_c]
step_pin: gpio10
dir_pin: gpio9 # If for some reason the motor is moving in the oppsite direction of what its supposed to, change this to "!gpio9"
enable_pin: !h616:gpio263 # H616-PI7
microsteps: 32
rotation_distance: 40
full_steps_per_rotation: 400
#   The number of full steps for one rotation of the stepper motor.
#   Set this to 200 for a 1.8 degree stepper motor or set to 400 for a
#   0.9 degree motor. The default is 200.
endstop_pin: ^h616:gpio269 # H616-PI13
homing_speed: 80
position_endstop: 142 # If you are building a taller or shorter Delta Flyer, change this to fit your build size.
angle: 90.000000
arm_length: 150
homing_retract_dist: 10
second_homing_speed: 5

# MORE INFO:  https://www.klipper3d.org/Config_Reference.html#tmc2209
[tmc2209 stepper_c]
uart_pin: gpio1
tx_pin: gpio0
run_current: 0.9 # This sets the amunt of power sent to the motor. If your motors are too hot, lower this value, if the motor is skipping steps, increase the value. Make sure this wont go too high, it can damage components.
interpolate: true
uart_address: 1
#stealthchop_threshold: 999999 # Uncomment to enable Stealthchop

#==================================#
#   EXTRUDER
#==================================#
# These lines sets all the parameters
# for the extruder and hotend. these
# wont need to change unless you are
# installing a mod that changes any
# part of the toolhead of the printer.
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

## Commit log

2025-10-09 Add files via upload
    add wiring diagram
2025-10-09 Add files via upload
    Update wiring diag
2025-10-09 Add Delta Flyer Refit website
    [Delta_Flyer_Buildplate_150.stl, printer.cfg]
2025-10-12 Rename Delta Flyer Refit Wiring Diagram.pdf to Delta Flyer Wiring Diagram.pdf
2025-10-12 Rename Rolohaun Delta Flyer Refit - 0.4mm Nozzle.orca_printer to Rolohaun Delta Flyer - 0.4mm Nozzle.orca_printer
2025-10-12 Update index.html
    remove bed texture from displayed images
2025-10-12 add backup folder
    [Delta_Flyer_Buildplate_150.stl, printer.cfg]
2026-06-06 Create klipper_mcu
